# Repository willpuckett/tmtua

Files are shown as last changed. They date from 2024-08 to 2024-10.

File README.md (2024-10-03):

# TMTua

A drop-in fan connector for your Quiet Storm.

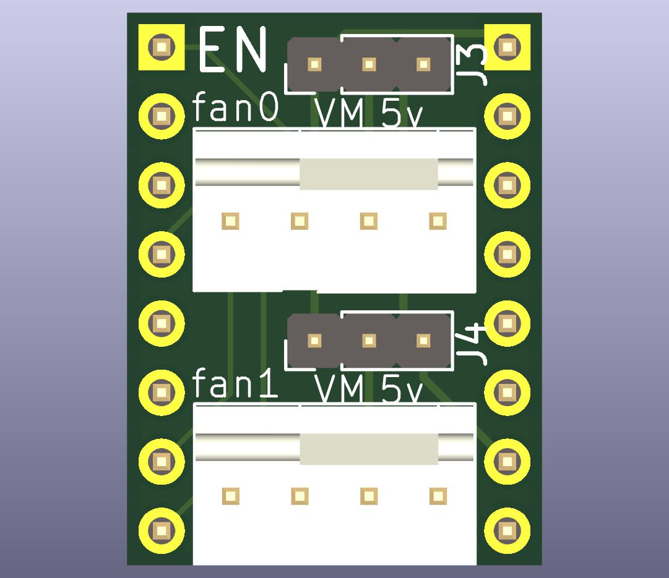
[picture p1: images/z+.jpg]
TMTua


TMTua is smallish board with a single purpose: to connect a 4 pin (Noctua) fan
to your printer pcb without having to crimp a custom cable ever again.

## Features

- 3/4 pin fan connector
- No soldering required
- Voltage selection jumper (5V or Motor Voltage)

## Usage

1. Install the TMTua in a spare stepper driver slot on your printer pcb. Make
   sure the orientation is correct by aligning the top silk screen that says
   "EN" with the stepper driver slot's enable pin. If you install this
   backwards, bad things™ will happen.
2. Connect the fan to the TMTua using the 4 pin connector.
3. Set the voltage jumper to the desired voltage (5V or Motor Voltage). There is
   no buck on board, so if you have a 24V printer, you CANNOT use a 12V fan.
4. Match your stepper slot's pin numbers to the TMTua's pin numbers using the
   following table and your PCB's schematic/pinout diagram in your printer
   firmware.

| TMTua Pin | Stepper Driver Pin |
| --- | --- |
| fan0 | |
| tach0 | EN |
| tach1 | UART[^1] |
| fan1 | |
| pwm0 | STEP |
| pwm1 | DIR |

## Example Klipper Configuration

```
[fan_generic fan_1]
pin: PA1
tachometer_pin: ^PD8
```

## Tachometer Pull-ups

You can use the
[Noctua white paper](https://noctua.at/pub/media/wysiwyg/Noctua_PWM_specifications_white_paper.pdf)
to assess whether the onboard pull-up if there's already one on the EN pin is
sufficient for the tach pins and your fans.

The paper outlines the following **minimum** recommendations:

| Voltage | Pullup Resistor(Ω) |
| --- | --- |
| 5V | 1k |
| 12V | 2k7 |
| 24V | 12k |

For example, the internal pull-ups on STM32F407 are about 40k which are
sufficient for all cases, but the hardware 10k pull-up on EN on my Robin Nano v3
board is too strong for a 24v fan, though fine for 5 and 12v fans.

## Schematic

Schematic

## Where Do I Get One?

You can order the board from [JLCPCB](https://jlcpcb.com) using the
[production_files](jlcpcb/production_files) directory.

They're also available on my [here](https://octule.com).

[^1]: May not be wired on older boards. On newer boards, you may need to jumper
the UART pin under the stepper driver slot to connect it to your mcu. Consult
your board's schematic for more information.

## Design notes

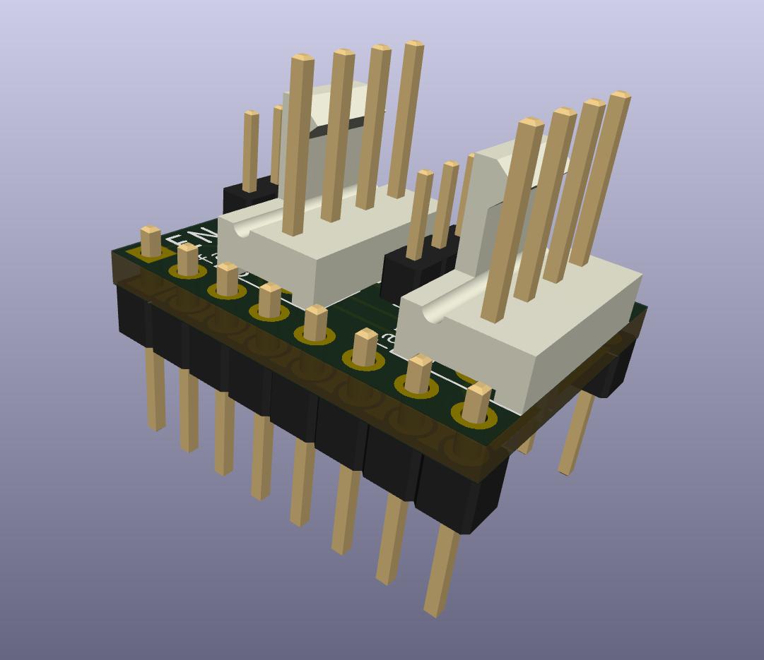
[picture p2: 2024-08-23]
images/corner.jpg

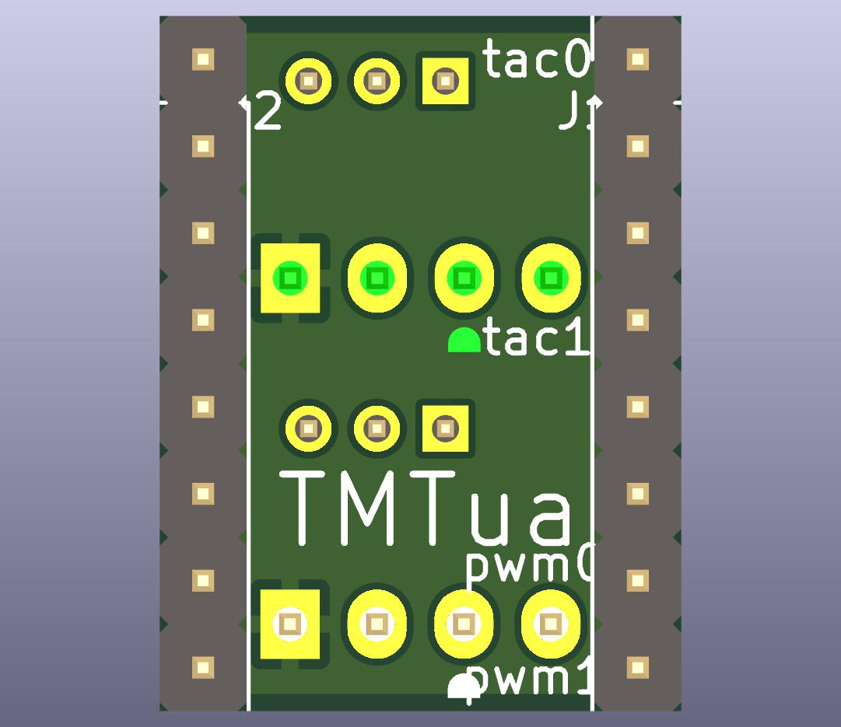
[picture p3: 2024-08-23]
images/z-.jpg

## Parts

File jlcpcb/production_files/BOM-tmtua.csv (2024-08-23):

Comment | Designator | Footprint | LCSC
B-2100S08P-A110 | J1,J2 | PinHeader_1x08_P2.54mm_Vertical | C124381
HF1004E | CN1,CN2 | FanPinHeader_1x04_P2.54mm_Vertical | C2761402
PZ200V-11-03P | J3,J4 | PinHeader_1x03_P2.00mm_Vertical | C541857

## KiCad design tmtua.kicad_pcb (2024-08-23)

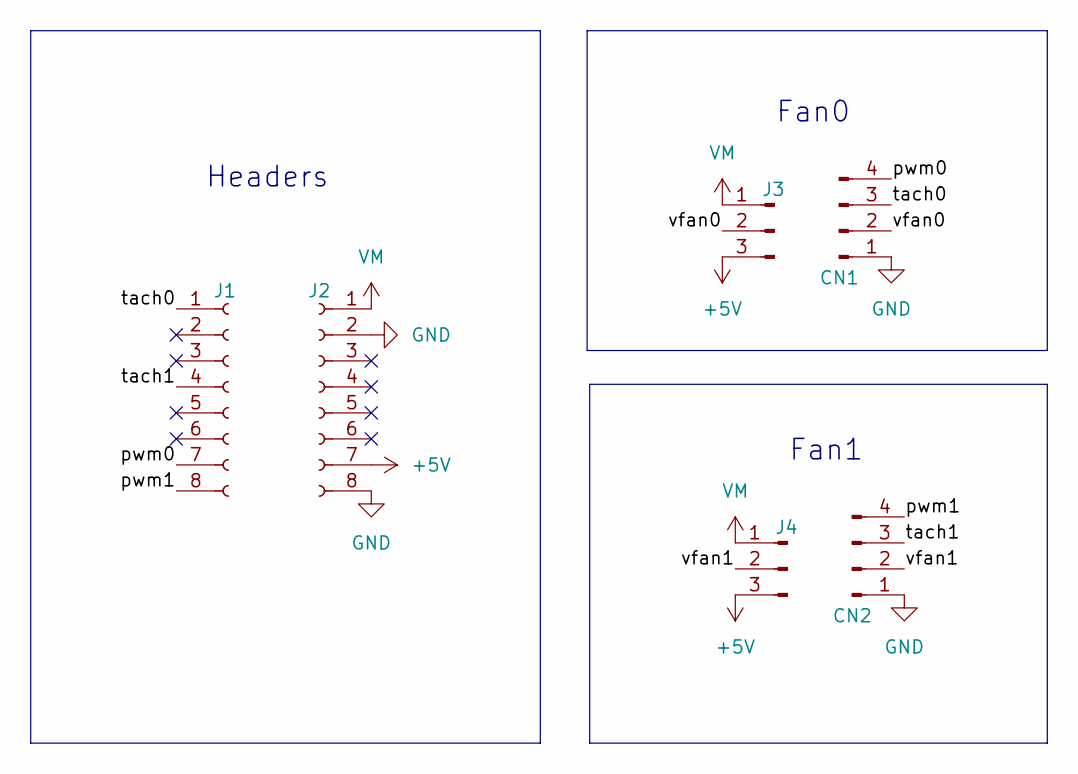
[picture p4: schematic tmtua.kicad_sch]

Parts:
CN1, CN2: HF1004E; FanPinHeader_1x04_P2.54mm_Vertical
J1, J2: B-2100S08P-A110; PinHeader_1x08_P2.54mm_Vertical
J3, J4: PZ200V-11-03P; PinHeader_1x03_P2.00mm_Vertical

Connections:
+5V: J2.7, J3.3, J4.3
/pwm0: CN1.4, J1.7
/pwm1: CN2.4, J1.8
/tach0: CN1.3, J1.1
/tach1: CN2.3, J1.4
/vfan0: CN1.2, J3.2
/vfan1: CN2.2, J4.2
GND: CN1.1, CN2.1, J2.2, J2.8
VM: J2.1, J3.1, J4.1

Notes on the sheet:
Fan1
Fan0
Headers

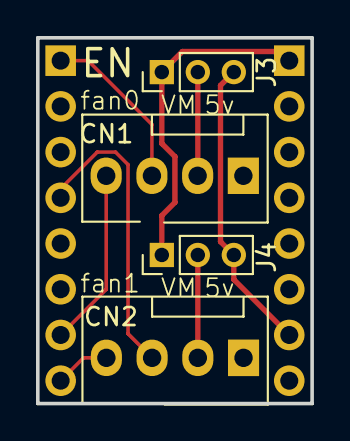
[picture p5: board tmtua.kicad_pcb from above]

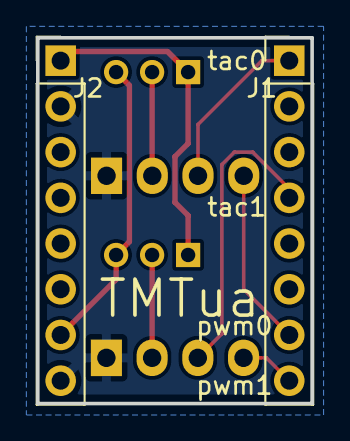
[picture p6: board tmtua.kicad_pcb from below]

Board: 2 copper layers, 15.2 x 20.3 mm, 6 parts (2 on the bottom side), 9 nets.
